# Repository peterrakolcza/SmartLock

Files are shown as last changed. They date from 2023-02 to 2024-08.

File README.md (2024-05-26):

# 🔒 Smart Lock with Home Key support🔒



A smart lock built using ESP8266, an affordable microcontroller with WiFi capabilities, that can be controlled through a mobile app or web interface.

### Features

- 📱 Remote control of lock through app or web interface
- 🔐 Smart home integration like Homebridge.
- 🕰️ Real-time status updates
- 💳 Optional Home Key support
- 🔨 Easy installation, compatible with most standard locks

<br>

## 💭 Inspiration

The whole idea came from a [hackaday.io](https://hackaday.io/project/11917-smart-lock) project, huge thanks for providing the basic STL files and logic. I tried to further improve the project and make it possible to integrate it into existing smart home ecosystems like Apple HomeKit.

### **Furthermore, the objectives were almost identical:**

- Device must be cheap. This means no expensive motors or sensors can be used.
- Device must be presentable. I don't want to see any cables, electronics not even the motor itself on my apartment door (since it is a very small apartment).
- No modifications on door itself. I am a tenant at this apartment right now so I can't modify anything that can't be fixed.
- It should be secure. Most of the RF devices are vulnerable to replay attacks, the lock should be safe enough.

| Inspiration - hackaday.io | Latest version |
| :---: | :---: |
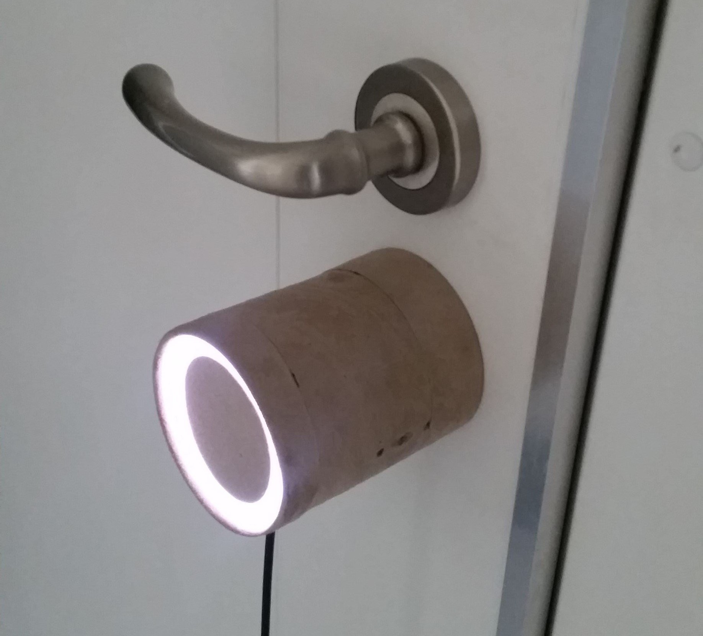
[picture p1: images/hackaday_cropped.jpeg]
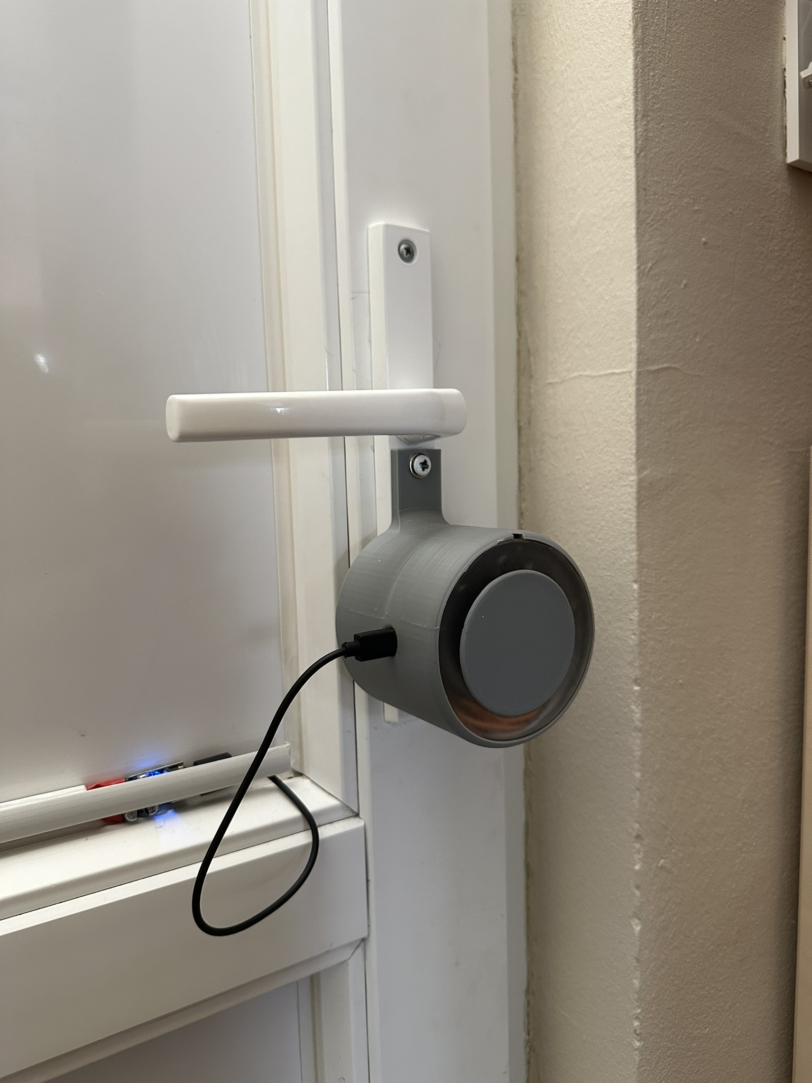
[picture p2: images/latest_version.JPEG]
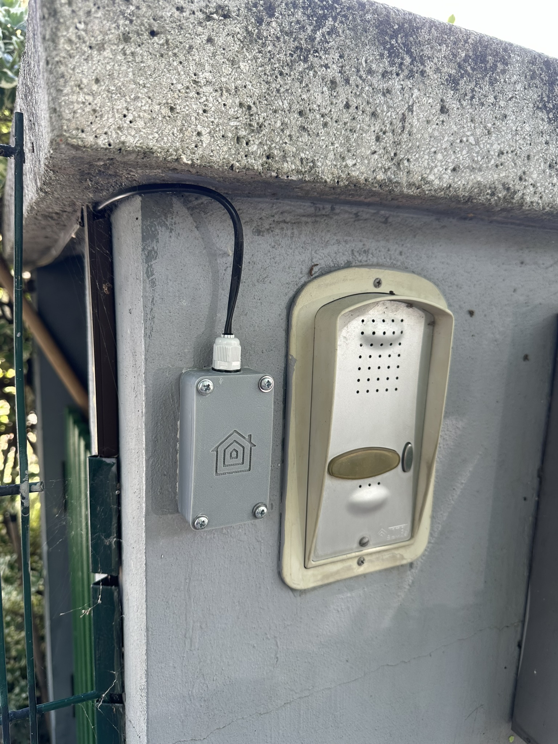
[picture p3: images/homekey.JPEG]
|  |   |

<br>

## 🚀 Getting Started

1. Clone the repository to your local machine.

```bash
git clone https://github.com/peterrakolcza/SmartLock.git
```

2. 3D print the selected models
3. Order the custom PCB and the components from JLCPCB for example
4. Wait :(
5. Configure the parameters in the code
```
#ifndef STASSID
#define STASSID "*****" // CHANGE THIS
#define STAPSK  "*****" // CHANGE THIS
#endif

struct { 
  const int numberOfTurnsRequired = 2; // CHANGE THIS
  // CALIBRATE
  int TimeToLock = 1000;
  int TimeToUnlock = 1000;
} settings;
```
6. Flash the firmware
7. Assemble the whole lock
8. Calibration: 
     -  it is highly recommended to calibrate the smart lock at first boot by holding down side-button while powering it on. 
     - Before the calibration it will flash 3 times. 
     - After that it will try to lock the door until the user presses the side-button. 
     - It will flash 3 times again. 
     - Finally, it will try to unlock the door until the button is pressed. 
     - It will flash 3 times to indicate the end of the calibration process.
     - The smart lock now registered and saved the amount of time required to lock / unlock the door.
9. Integrate it into your existing smart home ecosystem using the API function or Homebrige with / without Home Key support

<br>

## ⚡ Custom PCB

You can just order my custom PCB assembled and flash the firmware. After that, connecting the sensors and servo using the header pins are easy.

<br>

| easyEDA | PCB |
| :---: | :---: |
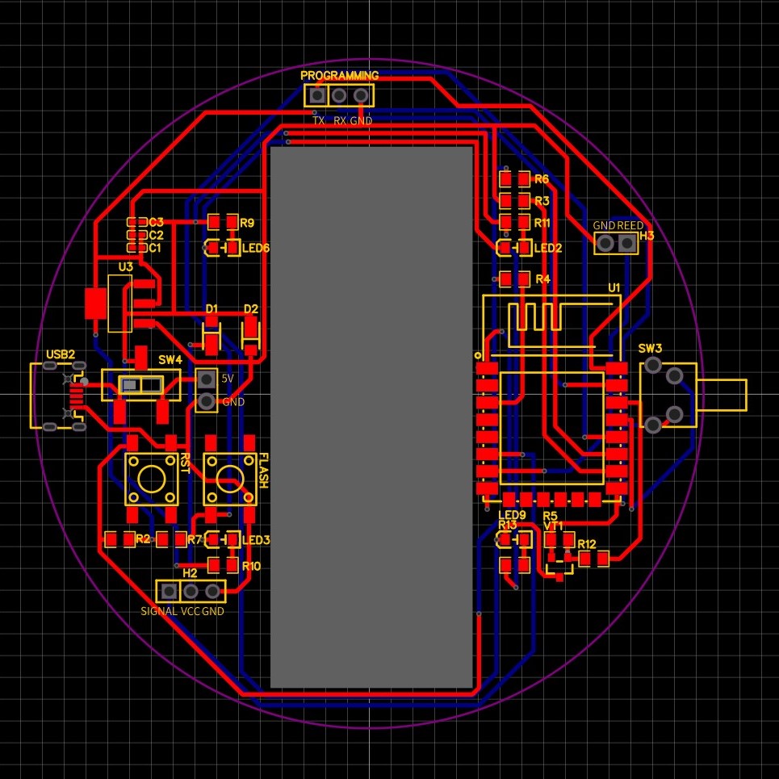
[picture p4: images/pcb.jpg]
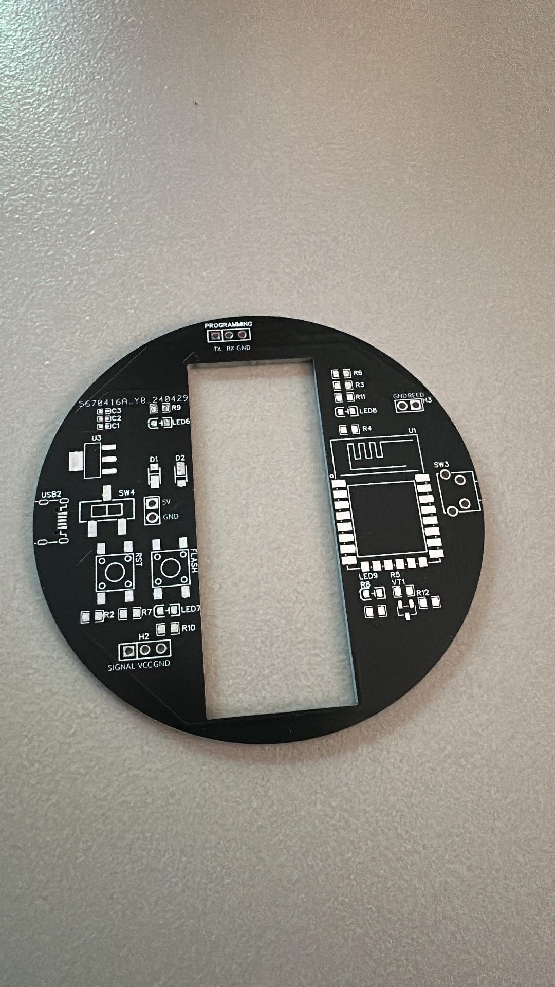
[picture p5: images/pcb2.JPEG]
|  |  |

<br>

## 🔌 Pinout

<br>

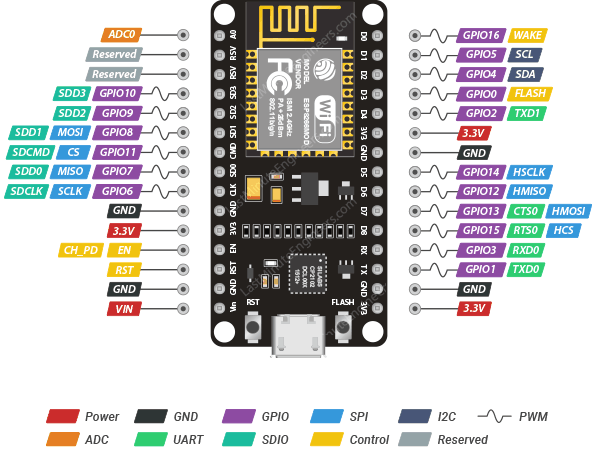
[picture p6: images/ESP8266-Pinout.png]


| Pin on ESP | Pin in code |  Funcionality  |
| :---: | :---: | :---: |
| D6 | 12 |  Servo signal  |
| D7 | 13 |  Reed sensor |
| D2 | 4 | Button |
| D1 | 5 | LED |

<br>
<br>
<br>
<br>
<br>
<br>
<br>
<br>

## ⚠️ **Limitations**

A lift-up handle on a smart lock can introduce several challenges that affect usability, compatibility, and security. One primary issue is user convenience. The necessity to lift the handle adds an extra step to the process of locking or unlocking the door, which can be particularly inconvenient when users' hands are full, they are in a hurry, or when it's dark. This could prevent the smart lock to properly lock the door.

_A future feature is planned to solve this issue, by automatically falling back to unlocked state when locking failed._

<br>

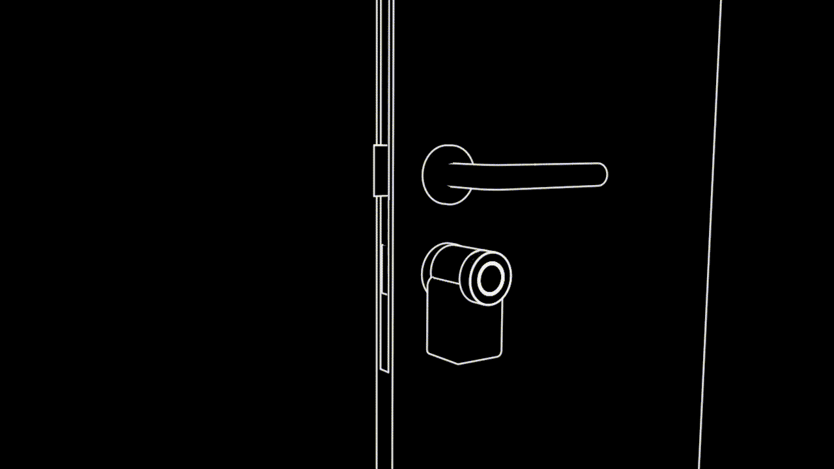
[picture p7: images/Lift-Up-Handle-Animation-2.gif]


<br>

## 📙 API

Example request to lock the door:

```bash
curl -X POST http://smartlock.local -H 'Content-Type: application/json' -d '{"state":"locked"}'
```

Example request to get the current state:

```bash
curl -X GET http://smartlock.local
```

Example response:

```json
{
  "state": "locked"
}
```

<br>

## 🏠 Homebridge integration

<br>

<p align="center">

</p>

Homebridge allows you to integrate with smart home devices that do not natively support HomeKit. There are over 2,000 Homebridge plugins supporting thousands of different smart accessories.

Homebridge is a lightweight Node.js server you can run on your home network that emulates the iOS HomeKit API. It supports Plugins, which are community-contributed modules that provide a basic bridge from HomeKit to various 3rd-party APIs provided by manufacturers of "smart home" devices.

You have 2 options to integrate the smart lock to your existing Apple HomeKit smart home:

### Home Key

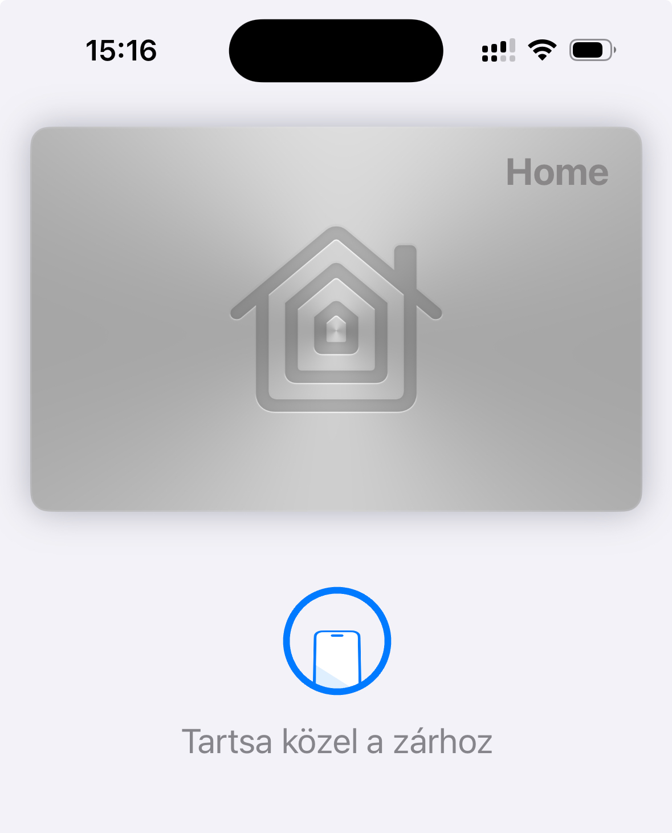
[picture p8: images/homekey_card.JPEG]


This all made possible by this project: [apple-home-key-reader](https://github.com/kormax/apple-home-key-reader) , thanks to [kormax](https://github.com/kormax). Furthermore, thanks for [nagolnad](https://github.com/nagolnad) for a [OrangePi Zero 2W Implementation](https://github.com/kormax/apple-home-key-reader/discussions/14) which was a great starting point!

Their project offers a demonstration of an Apple Home Key Reader built in Python. It includes:

- Fully functional Apple Home Key NFC authentication;
- NFC Express mode support;
- HAP configuration (as a virtual lock)

It's intended for makers and developers interested in building practical and user-friendly applications using this example.

To add Home Key support to this smart lock:
1. 3D print the case included in the repository
2. follow this guide: [OrangePi Zero 2W Implementation](https://github.com/kormax/apple-home-key-reader/discussions/14)
3. use the modified code included in the repository to make it compatible with this lock 

<br>

### EspLock

The lock uses the [EspLock](https://github.com/volca/homebridge-esplock) Homebridge plugin to integrate it into the Apple HomeKit ecosystem. Huge thanks to [volca](https://github.com/volca)!

Example configuration, it is possible to use a static IP address or the hostname:

```json
{
  "accessories": [
    {
      "accessory": "EspLock",
      "name": "Front Door",
      "url": "http://smartlock.local"
    }
  ]
}
```

To disable autolock feature, delete the following function from the index.js file:

```js
setTimeout(function () {
  if (currentState == Characteristic.LockTargetState.UNSECURED) {
    self.lockservice.setCharacteristic(
      Characteristic.LockTargetState,
      Characteristic.LockTargetState.SECURED
    );
  }
}, 5000);
```

<br>

## Contributions

🙏 I welcome contributions from the community! If you have any ideas or suggestions, please open an issue or submit a pull request.

<br>

## License

This project is licensed under the MIT License. See LICENSE for more information.

<br>

## 💻 Contact

For any questions or concerns, please open an issue or contact me.

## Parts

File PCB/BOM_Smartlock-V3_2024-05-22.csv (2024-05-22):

ID | Name | Designator | Footprint | Quantity | Manufacturer Part | Manufacturer | Supplier | Supplier Part | Price
1 | LED0805-RD_WHITE | LED6,LED2,LED3,LED9 | LED0805-RD_WHITE | 4 | TZ-P2-0805WYCS2-0.8T | TUOZHAN(拓展光电) | LCSC | C779456 | 0.01
2 | SOT-23_L2.9-W1.3-P1.90-LS2.4-BR | VT1 | SOT-23_L2.9-W1.3-P1.90-LS2.4-BR | 1 | 2N7002E-7-F | DIODES(美台) | LCSC | C151383 | 0.039
3 | R0805 | R10,R13,R11,R9 | R0805 | 4 | RS-05K66R5FT | FH(风华) | LCSC | C322549 | 0.002
4 | R0805 | R5 | R0805 | 1 | RC0805FR-0710KL | YAGEO(国巨) | LCSC | C84376 | 0.002
5 | R0805 | R12 | R0805 | 1 | CRCW0805100RJNEAC | VISHAY(威世) | LCSC | C3008930 | 0.008
6 | SW-SMD_SHOUHAN_MST-22D18G23J_C2875122 | SW4 | SW-SMD_SHOUHAN_MST-22D18G23J_C2875122 | 1 | MST-22D18G2 3J | SHOU HAN(首韩) | LCSC | C2875122 | 0.077
7 | PZ254V-11-03P_C2937625 | PROGRAMMING,H2 | HDR-TH_3P-P2.54-V-M | 2 | PZ254V-11-03P | XFCN(兴飞) | LCSC | C2937625 | 0.014
8 | PZ254V-11-02P | H3,H5 | HDR-TH_2P-P2.54-V-M | 2 | PZ254V-11-02P | XFCN(兴飞) | LCSC | C492401 | 0.012
9 | PTS645SH50SMTR92LFS | RST,FLASH | KEY-SMD_4P-L6.0-W6.0-P4.50-LS9.0 | 2 | PTS645SH50SMTR92LFS | C&K | LCSC | C221869 | 0.553
10 | DTSA-65N-V | SW3 | SW-TH_DTSA-65N-V | 1 | DTSA-65N-V | 圜达 | LCSC | C224975 | 0.114
11 | SBR3M30P1-7 | D1,D2 | POWERDI123_L2.8-W1.8-LS3.7-RD | 2 | SBR3M30P1-7 | DIODES(美台) | LCSC | C460953 | 0.108
12 | 10kΩ | R2,R3,R4,R6,R7 | R0805 | 5 | 0805W8F1002T5E | UNI-ROYAL(厚声) | LCSC | C17414 | 0.002
13 | 100nF | C1 | C0402_NEW | 1 | CL05B104KO5NNNC | SAMSUNG(三星) | LCSC | C1525 | 0.001
14 | 2.4GHz | U1 | WIFIM-SMD_ESP-12F-ESP8266MOD | 1 | ESP-12F(ESP8266MOD) | Ai-Thinker(安信可) | LCSC | C82891 | 2.031
15 | 10uF | C2,C3 | C0402 | 2 | CL05A106MP5NUNC | Samsung Electro-Mechanics | LCSC | C315248 | 0.008
16 | AMS1117-3.3_C347222 | U3 | SOT-223-4_L6.5-W3.5-P2.30-LS7.0-BR | 1 | AMS1117-3.3 | Youtai Semiconductor Co., Ltd. | LCSC | C347222 | 0.036
17 | MICRO-11-G5P3-A1T2 | USB2 | MICRO-USB-SMD_MICRO-12-G2P3-A1T2 | 1 | MICRO-11-G5P3-A1T2 | Yuandi(台湾元迪) | LCSC | C2874592 | 0.074

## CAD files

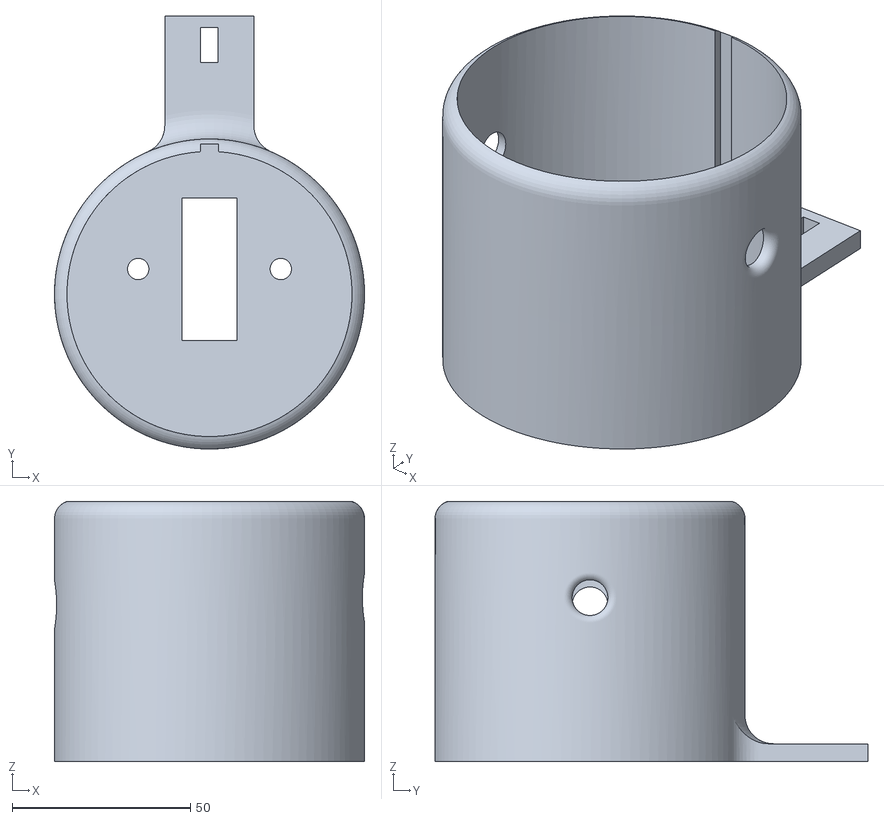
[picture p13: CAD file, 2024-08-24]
3D printed case/bottom.stl
87.0 x 121.5 x 73.0

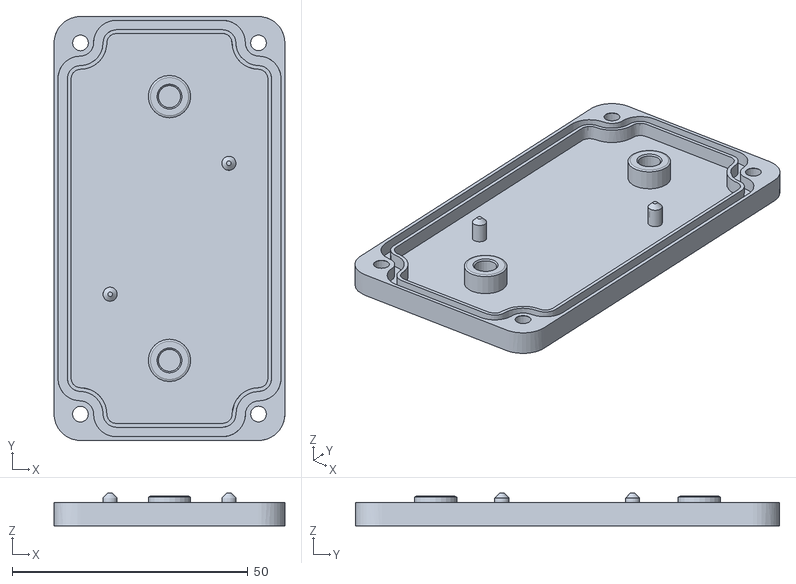
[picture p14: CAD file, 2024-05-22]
homekey/3D printed case/lid-with-homekit-logo-in-portrait.stl
49.0 x 90.0 x 6.97

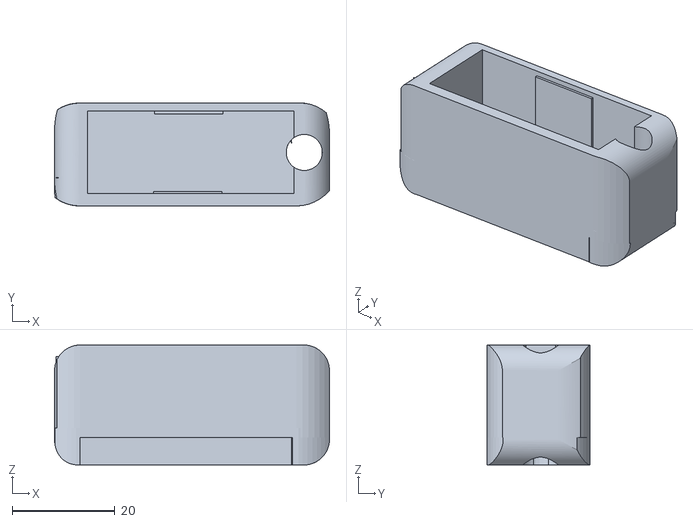
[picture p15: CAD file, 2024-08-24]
3D printed case/doorknob_servo_adapter.stl
53.4 x 20.0 x 23.3

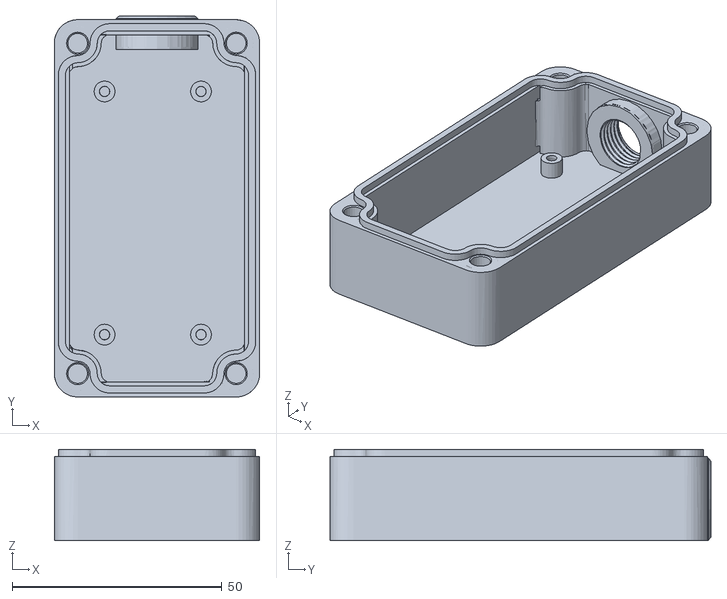
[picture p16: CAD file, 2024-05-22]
homekey/3D printed case/enclosure-with-pg7-hub.stl
49.0 x 90.9 x 21.7

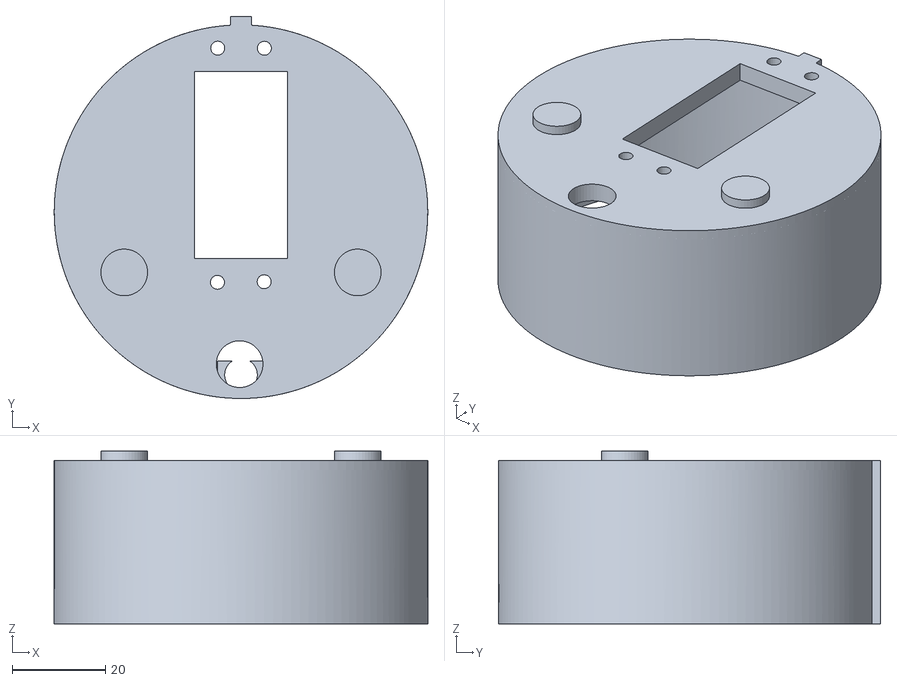
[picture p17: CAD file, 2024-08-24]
3D printed case/middle.stl
80.0 x 81.8 x 37.0

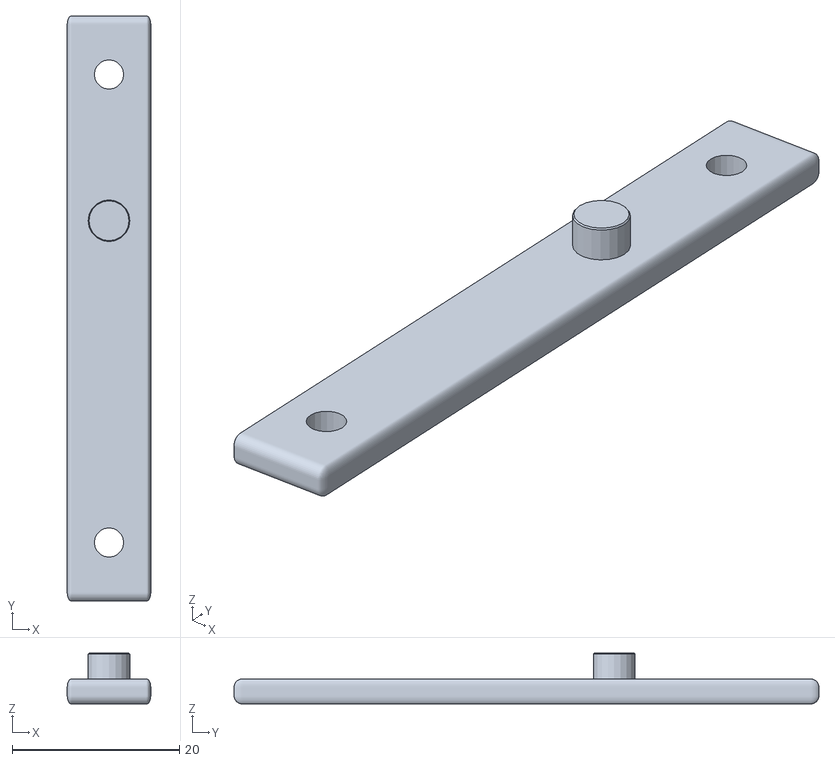
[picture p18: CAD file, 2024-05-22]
homekey/3D printed case/nfc-hold-down.stl
10.0 x 70.0 x 6.10

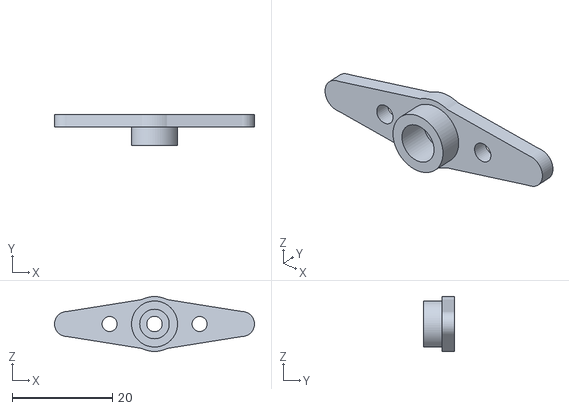
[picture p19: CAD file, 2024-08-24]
3D printed case/servo_horn_optional.stl
40.0 x 6.20 x 11.0

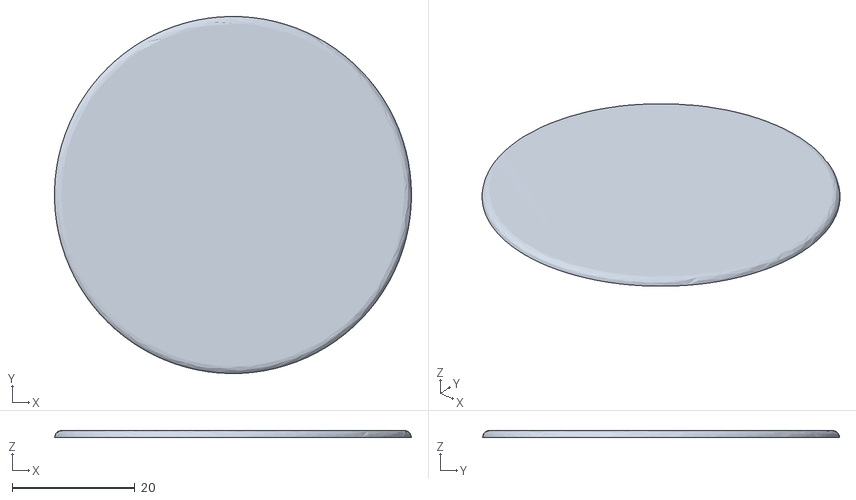
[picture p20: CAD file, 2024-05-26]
3D printed case/cover_led.stl
58.2 x 58.3 x 1.17

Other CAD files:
3D printed case/Fusion files/bottom v20.f3z
3D printed case/Fusion files/doorknob_servo_adapter v3.f3d
3D printed case/Fusion files/middle v9.f3z

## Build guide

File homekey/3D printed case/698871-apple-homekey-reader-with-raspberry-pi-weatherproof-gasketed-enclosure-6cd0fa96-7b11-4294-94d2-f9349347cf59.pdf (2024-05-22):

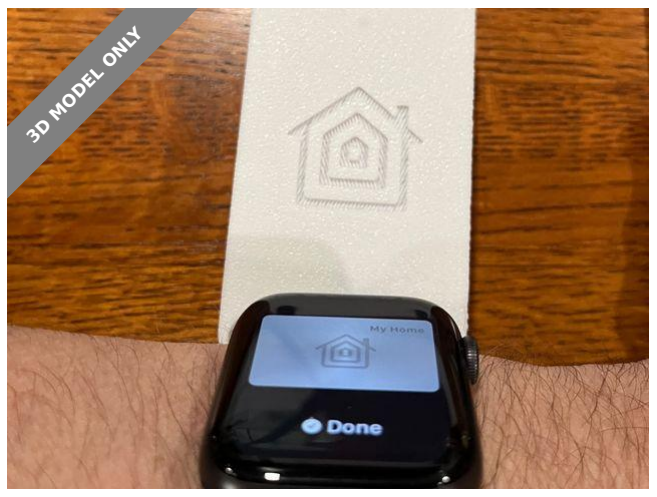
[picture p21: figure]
3D MODEL ONLY

## Summary

Enclosure to hold a PN532 NFC reader and a Raspberry Pi Zero 2 W for the purpose of reading an Apple HomeKey,

Hobby & Makers (https://printables.com/model?categoryId=48) > Electronics (https://printables.com/model?categoryId=52)

Video of this project working:

This enclosure is intended to hold a PN532 NFC reader along with a Raspberry Pi Zero 2 W for the purpose of reading an Apple HomeKey to unlock or open a door. I'm running the software found here and interfacing with Home Assistant: https://github.com/kormax/apple-home-key-reader

To build this item, you need to print (3) parts: a lid, an enclosure and the hold down for the NFC reader.

There are STLs for the base enclosure with and without a threaded hub. The hub has PG7 threads to accept a cable gland or other fitting. There are no provisions included for mounting the enclosure. You could drill it or add tabs to accept screws. I am using outdoor 3M dual lock tape so that I can remove this project without damage if I wish to at a later date.

Patrick O'Neal (https://printables.com/@PatrickONeal_471773)

## Apple HomeKey

## Reader with

## Raspberry Pi

## Weatherproof

## Gasketed Enclosure

VIEW IN BROWSER (https://printables.com/model/698871-apple-homekey-reader-with-raspberry-pi-weatherproo)

updated 30. 12. 2023 | published 30. 12. 2023

I'm using this to open my garage door. I couldn't think of a particularly good way to get the power cable from the outside to the inside other than removing the garage door trim and routing a slot in the back of it. I did this by hand on my router table and ran the slot slightly uphill to discourage water intrusion.

I have not printed the enclosure without the threaded hub, but it should be fine.

I printed the hold down and lid face down with supports in the countersinks for the screws.

I did not need any supports for the base enclosure.

The inside corners of the enclosure have a few abnormalities that I think were caused by using the source OpenSCAD file to product such a small enclosure. These have not caused any compromise in the integrity of the enclosure that I can detect.

The two holes on the inside of the cover intended to accept heat-set inserts are shallow. The inserts will fit, but the soldering iron tools to set them with are usually long enough that you might burn through the front cover if you are not cautious. Be careful and the inserts with fit without damaging the cover.

The bill of materials is as follows:

Electronics:
1x Raspberry Pi Zero 2 W
1x PN532 NFC reader
1x USB cable or other cable for the 5V power supply
1x USB-A power supply or other regulated 5V power supply
4x Short lengths of small gauge wire to connect the NFC reader to the Pi

Hardware
1x Cable tie to serve as a strain relief for the power cable
1x PG7 Cable Gland with gasket/o-ring. Make sure it's an appropriate size for your power cable
6x M3x5x4 Heatset Inserts, 2 for the lid and 4 for the enclosure
4x M3 x 8mm screws for front cover. Can be socket head or button head-stainless would be better for outdoors
4x M2.5 x 5mm screws for Pi, I used socket head, but button head would likely work. Do not over-tighten, threaded into plastic.
2x M3 x 6mm screws for NFC reader strap, button head . Socket head might interfere with Pi, but maybe not.
2mm silicone rubber round gasket cord to help weather proof enclosure lid

## Model files

## This remix is based on

Threaded PG9 and PG7 Gland Inserts for 3/4" Conduit Box
by forkineye (https://www.thingiverse.com/thing:3891986)

Stable and waterproof electronic box / enclosure (https://printables.com/model/72839-stable-and-waterproof-electronic-box-enclosure) by pb-tec (https://printables.com/@pbtec_14016)

HomeKey PN532 case (https://printables.com/model/673192-homekey-pn532-case)
by MohammadAG (https://printables.com/@MohammadAG_237916)

lid-with-homekit-logo-in-portrait.stl

nfc-hold-down.stl

enclosure-with-pg7-hub.stl

lid-with-homekit-logo-in-landscape.stl

lid-with-no-logo.stl

## License

This work is licensed under a
Creative Commons (4.0 International License)

Attribution—Noncommercial—Share Alike (http://creativecommons.org/licenses/by-nc-sa/4.0/)

✖ | Sharing without ATTRIBUTION
✔ | Remix Culture allowed
✖ | Commercial Use
✖ | Free Cultural Works
✖ | Meets Open Definition

enclosure-with-no-hub.stl

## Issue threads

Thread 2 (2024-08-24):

homebridge-esplock is deprecated

peterrakolcza, 2024-08-24:
### Issue Description
The homebridge-esplock plugin has been deprecated and is no longer maintained. Unfortunately, due to the deprecation of homebridge-esplock, we removed support for this Homebridge plugin as it requires statusCode and battery percentage in the API response.

This results in the smart lock not functioning correctly with this plugin, leading to a degraded user experience for those who rely on this.

### Proposed Solution
To resolve this issue, I suggest searching for an alternative Homebridge plugin that is actively maintained and implementing support for it within the smart lock's API.

### Steps to Reproduce

1. Install and configure homebridge-esplock.
2. Attempt to control the smart lock using the plugin.
3. Observe that the plugin fails due to an incompatible JSON response format.

### Expected Behavior
The smart lock should provide a compatible JSON response in the following format:

### Actual Behavior
The current JSON response does not match the format expected by homebridge-esplock, causing functionality issues.

### Temporary Workaround
As a temporary workaround, users can switch to using the homebridge-http-lock-ultimate plugin. This plugin is compatible with the smart lock's current API; however, it does not query for state updates. This means that if the lock is manually operated (e.g., by pressing a physical button), the state change will not be reflected in the Homebridge app.

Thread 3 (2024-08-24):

Screwless Smart Lock Design Using Double-Sided Tape

peterrakolcza, 2024-08-24:
### Enhancement Description

It would be beneficial to introduce a new version of the smart lock that does not require screws for installation and is instead held in place by strong double-sided tape. This design would provide a more user-friendly installation process, especially for those who are renting or prefer not to drill holes into their doors.

### Rationale

The current smart lock design requires screws for installation, which can be cumbersome and may deter some users, particularly those in rental properties where modifications to doors are not allowed. A version that uses double-sided tape instead would offer the following benefits:

- **Easy Installation:** No tools or drilling required, making it accessible for users with limited DIY experience.
- **Universal:** The current design of the lock fits a limited number of locks or requires small adjustments which could be dealbreaker. Introducing a screwless version would be more universal.

### Proposed Implementation

1. **Design Modification:** Modify the lock's outer shell to include areas suitable for the application of industrial-strength double-sided tape.
2. **Testing:** Ensure that the adhesive used is strong enough to hold the lock securely over long periods and through regular use.
3. **Instructions:** Provide clear installation instructions and warnings about surface preparation to ensure the tape adheres properly.

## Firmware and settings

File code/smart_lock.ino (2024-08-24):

#include <ESP8266WiFi.h>
#include <ESP8266WebServer.h>
#include <ArduinoJson.h>
#include <Servo.h>
#include <ESP8266mDNS.h>
#include <EEPROM.h>

int baseVersion = 3;

#define SERVOPIN 12
#define SENSOR 13
#define BUTTON 4
#define RINGLED 5

Servo servo;

int counter = 0;

//#############################################################################################################################################
//###                                                                   ###
//###                             CONFIGURATION                         ###
//###                                                                   ###
//#############################################################################################################################################

#ifndef STASSID
#define STASSID "*************" // CHANGE THIS
#define STAPSK  "*************" // CHANGE THIS
#endif

const int numberOfTurnsRequired = 1; // CHANGE THIS
bool previousStateWasHigh = true;

struct { 
  // CALIBRATE
  int TimeToLock = 1000;
  int TimeToUnlock = 1000;
} settings;

//#############################################################################################################################################
//###                                                                   ###
//###                             LOCK                                  ###
//###                                                                   ###
//#############################################################################################################################################
bool locked = true;
bool lockingInProgress = false;
bool unlockingInProgress = false;
unsigned long lockUnlockStartTime = 0;

void lock() {
  if (!locked && !lockingInProgress) {
    servo.attach(SERVOPIN);
    servo.write(180);
    lockUnlockStartTime = millis();
    lockingInProgress = true;
  }
}

void unlock() {
  if (locked && !unlockingInProgress) {
    servo.attach(SERVOPIN);
    servo.write(1);
    lockUnlockStartTime = millis();
    unlockingInProgress = true;
  }
}

void handleLockUnlock() {
  if (lockingInProgress && millis() - lockUnlockStartTime >= settings.TimeToLock) {
    servo.detach();
    locked = true;

    // Completed the unlock, reset every state related variable
    counter = 0;
    previousStateWasHigh = false;
    
    
    if (lockingInProgress && millis() - lockUnlockStartTime >= settings.TimeToLock + 1000) lockingInProgress = false;
  }
  
  if (unlockingInProgress && millis() - lockUnlockStartTime >= settings.TimeToUnlock) {
    servo.detach();
    locked = false;

    // Completed the unlock, reset every state related variable
    counter = 0;
    previousStateWasHigh = false;
    
    if (unlockingInProgress && millis() - lockUnlockStartTime >= settings.TimeToUnlock + 1000) unlockingInProgress = false;
  }
}

//#############################################################################################################################################
//###                                                                   ###
//###                             WEBSERVER                             ###
//###                                                                   ###
//#############################################################################################################################################

const char* ssid = STASSID;
const char* password = STAPSK;

ESP8266WebServer server(80);

void handleNotFound() {
  String message = "File Not Found\n\n";
  message += "URI: ";
  message += server.uri();
  message += "\nMethod: ";
  message += (server.method() == HTTP_GET) ? "GET" : "POST";
  message += "\nArguments: ";
  message += server.args();
  message += "\n";
  for (uint8_t i = 0; i < server.args(); i++) {
    message += " " + server.argName(i) + ": " + server.arg(i) + "\n";
  }
  server.send(404, "text/plain", message);
}

void handleStatus() {
  char rsp[255];
  sprintf(rsp, "{\"state\":\"%s\"}", locked ? "locked" : "unlocked");

  server.send(200, "application/json", rsp);
}

void handleUpdate() {
  JsonDocument newjson;
  DeserializationError error = deserializeJson(newjson, server.arg("plain"));
  String state = newjson["state"];
  if (state == "") {
    int args = server.args();
    for (uint8_t i = 0; i < server.args(); i++) {
      String argName = server.argName(i);
      argName.toLowerCase();

      if (argName.equals("state")) {
        state = server.arg(i);
      }
    }

  }

  Serial.println(state);

  if (state != "null") {
    if (state == "locked") {
      if (!locked) {
        lock();

        char rsp[255];
        sprintf(rsp, "{\"success\":\"true\"}");
        server.send(200, "application/json", rsp);
      } else {
        char rsp[255];
        sprintf(rsp, "{\"success\":\"false\",\"error\":\"already locked\"}");
        server.send(200, "application/json", rsp);
      }
    }
    else if (state == "unlocked") {
      if (locked) {
        unlock();

        char rsp[255];
        sprintf(rsp, "{\"success\":\"true\"}");
        server.send(200, "application/json", rsp);
      } else {
        char rsp[255];
        sprintf(rsp, "{\"success\":\"false\",\"error\":\"already unlocked\"}");
        server.send(200, "application/json", rsp);
      }
      
    }

    server.send(400, "text/plain", "INVALID POST REQUEST");
  } else {
    server.send(400, "text/plain", "EMPTY POST REQUEST");
  }
}

//#############################################################################################################################################
//###                                                                   ###
//###                               SENSOR                              ###
//###                                                                   ###
//#############################################################################################################################################

void handleUpdateLockState() {
  if (digitalRead(SENSOR) == LOW && previousStateWasHigh) {
    counter++;
    previousStateWasHigh = false;
    delay(500);
  } else if (digitalRead(SENSOR) == HIGH) {
    previousStateWasHigh = true;
  }

  if (counter == numberOfTurnsRequired) {
    counter = 0;
    if (locked) {
      locked = false;
      Serial.println("unlocked manually");
    } else {
      locked = true;
      Serial.println("locked manually");
    }
  }
}

//#############################################################################################################################################
//###                                                                   ###
//###                             BUTTON                                ###
//###                                                                   ###
//#############################################################################################################################################

void handleButton() {
  if (digitalRead(BUTTON) == LOW) {
    if (locked) {
      unlock();
      Serial.println("unlocked using the button");
    } else {
      lock();
      Serial.println("locked using the button");
    }
    delay(500);
  }
}

//#############################################################################################################################################
//###                                                                   ###
//###                             WIFI                                  ###
//###                                                                   ###
//#############################################################################################################################################

void initWifi() {
  WiFi.mode(WIFI_STA);
  WiFi.begin(ssid, password);
  Serial.println("");

  // Wait for connection
  while (WiFi.status() != WL_CONNECTED) {
    delay(500);
    Serial.print(".");
  }
  Serial.println("");
  Serial.print("Connected to ");
  Serial.println(ssid);
  Serial.print("IP address: ");
  Serial.println(WiFi.localIP());
}

//#############################################################################################################################################
//###                                                                   ###
//###                             LED                                   ###
//###                                                                   ###
//#############################################################################################################################################

void handleLED() {
  if (!locked) {
    digitalWrite(RINGLED, HIGH);
  } else {
    digitalWrite(RINGLED, LOW);
  }
}

void flashLED() {
  digitalWrite(RINGLED, HIGH);
  delay(500);
  digitalWrite(RINGLED, LOW);
  delay(500);
  digitalWrite(RINGLED, HIGH);
  delay(500);
  digitalWrite(RINGLED, LOW);
  delay(500);
  digitalWrite(RINGLED, HIGH);
  delay(500);
  digitalWrite(RINGLED, LOW);
}

//#############################################################################################################################################
//###                                                                   ###
//###                             CALIBRATION                           ###
//###                                                                   ###
//#############################################################################################################################################

void calibrate() {
  Serial.println("Starting calibration...");
  flashLED();

  while (digitalRead(BUTTON) == LOW) {
    delay(50);
  }

  int startTime = millis();
  servo.attach(SERVOPIN);
  servo.write(180);
  while (digitalRead(BUTTON) == HIGH) {
    delay(50);
  }
  servo.detach();
  settings.TimeToLock = millis() - startTime - 1000;
  if (settings.TimeToLock >= 1 && settings.TimeToLock <= 10) Serial.println("New lock time: " + String(settings.TimeToLock) + " ms");
  else {
    settings.TimeToLock = 5000;
    Serial.println("Invalid lock time, resetting back to default: 5000 ms");
  }

  flashLED();

  startTime = millis();
  servo.attach(SERVOPIN);
  servo.write(1);
  while (digitalRead(BUTTON) == HIGH) {
    delay(50);
  }
  servo.detach();
  settings.TimeToUnlock = millis() - startTime - 1000;
  if (settings.TimeToUnlock >= 1 && settings.TimeToUnlock <= 10) Serial.println("New unlock time: " + String(settings.TimeToUnlock) + " ms");
  else {
    settings.TimeToUnlock = 5000;
    Serial.println("Invalid unlock time, resetting back to default: 5000 ms");
  }

  EEPROM.put(0, settings); //write data to array in ram 
  EEPROM.commit();  //write data from ram to flash memory. Do nothing if there are no changes to EEPROM data in ram
  
  flashLED();
}

//#############################################################################################################################################
//###                                                                   ###
//###                             MAIN                                  ###
//###                                                                   ###
//#############################################################################################################################################

void setup() {
  pinMode(SENSOR, INPUT_PULLUP);
  pinMode(BUTTON, INPUT_PULLUP);
  pinMode(RINGLED, OUTPUT);
  Serial.begin(9600);

  initWifi();

  server.on("/", HTTP_GET, handleStatus);
  server.on("/", HTTP_POST, handleUpdate);
  server.onNotFound(handleNotFound);

  server.begin();
  Serial.println("HTTP server started");

  if (MDNS.begin("smartlock")) {
    Serial.println("MDNS responder started");
  }

  EEPROM.begin(sizeof(settings));
  EEPROM.get(0, settings); //read data from array in ram and cast it into struct called settings
  Serial.println("Current lock time: " + String(settings.TimeToLock) + " ms");
  Serial.println("Current unlock time: " + String(settings.TimeToUnlock) + " ms");

  delay(3000);
  if (digitalRead(BUTTON) == LOW) {
    calibrate();
  }
}

void loop() {
  MDNS.update();
  handleLockUnlock();
  if (!lockingInProgress && !unlockingInProgress) {
    server.handleClient();
    handleUpdateLockState();
    handleButton();
  }
  handleLED();
}

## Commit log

2023-02-07 added V1 files
    [Spectacular Borwo.stl, Swanky Kup.stl, doorknob_servo_adapter.stl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]
2023-02-07 cleaned up the folder
    [Swanky Kup.stl, doorknob_servo_adapter.stl, wall_mount_optional.stl]
2023-02-10 small changes
    [doorknob_servo_adapter.stl]
2023-02-20 started PCB design
    [pcb.kicad_pcb, pcb.kicad_sch]
2023-02-21 updated the PCB
    [pcb.kicad_pcb, pcb.kicad_sch]
2023-02-22 finished PCB design
    [pcb.kicad_pcb, pcb.kicad_sch]
2023-02-25 updated PCB design
    [pcb.kicad_pcb, pcb.kicad_sch]
2023-06-05 testing V3
    [BOM_PCB_Smartlock_auto_route_2023-05-21.csv, BOM_PCB_Smartlock_auto_route_2023-06-05.csv, BOM_Smartlock_2023-05-20.csv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]
2024-05-22 adding files for V3 update
    [BOM_PCB_Smartlock_auto_route_2023-03-30.csv, BOM_PCB_Smartlock_auto_route_2023-05-21.csv, BOM_PCB_Smartlock_auto_route_2023-06-05.csv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]
2024-05-26 updated documentation for the latest version
    [cover_led.stl]
2024-05-26 added more source files
    [bottom v19.f3z, doorknob_servo_adapter v2.f3d, middle v7.f3z]
2024-08-24 small upgrades and bug fixes
    [bottom v19.f3z, bottom v20.f3z, bottom.stl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]
